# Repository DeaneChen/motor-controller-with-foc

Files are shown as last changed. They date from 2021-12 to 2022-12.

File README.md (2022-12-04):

<!--
 * @Author       : LuHeQiu
 * @Date         : 2021-12-08 13:26:15
 * @LastEditTime : 2022-12-04 19:14:46
 * @LastEditors  : LuHeQiu
 * @Description  : 
 * @FilePath     : \motor-controller-with-foc\README.md
 * HomePage     : https://luheqiu.com
-->
<div align="center">
    <br/>
    <h1>
        <a href="https://www.luheqiu.com" target="_blank" rel="noopener noreferrer">
        LuHeQiu Logo
        </a>
    </h1>
    <strong>路何求创想工坊出品 | 硬件&算法工坊</strong>
</div>

# 【FOC+STM32】双路直流无刷电机矢量控制器-使用文档

<p align="center">
    
    
    
    
    
</p>

## 📕 介绍
控制器主控芯片采用STM32F405RGT6，控制器底层基于HAL库和FreeRTOS实时操作系统，预留CAN、USART、SWD、USB接口各一，便于通信和控制的工程应用。该控制器提供双路无刷电机控制，同时分别预留编码器接口与电压采样接口，适合于有感FOC与无感FOC的控制应用或算法验证。同时该控制板还可以适合于异步电机的矢量控制。

> **注意：此项目为硬件设计与算法验证项目，当前正处于设计和验证阶段，未进行完善的工程应用测试和极限参数的压力测试，请勿直接使用，以避免出现安全问题和财产损失，后续的验证情况会同步更新**

### 演示图片

<p align="center">
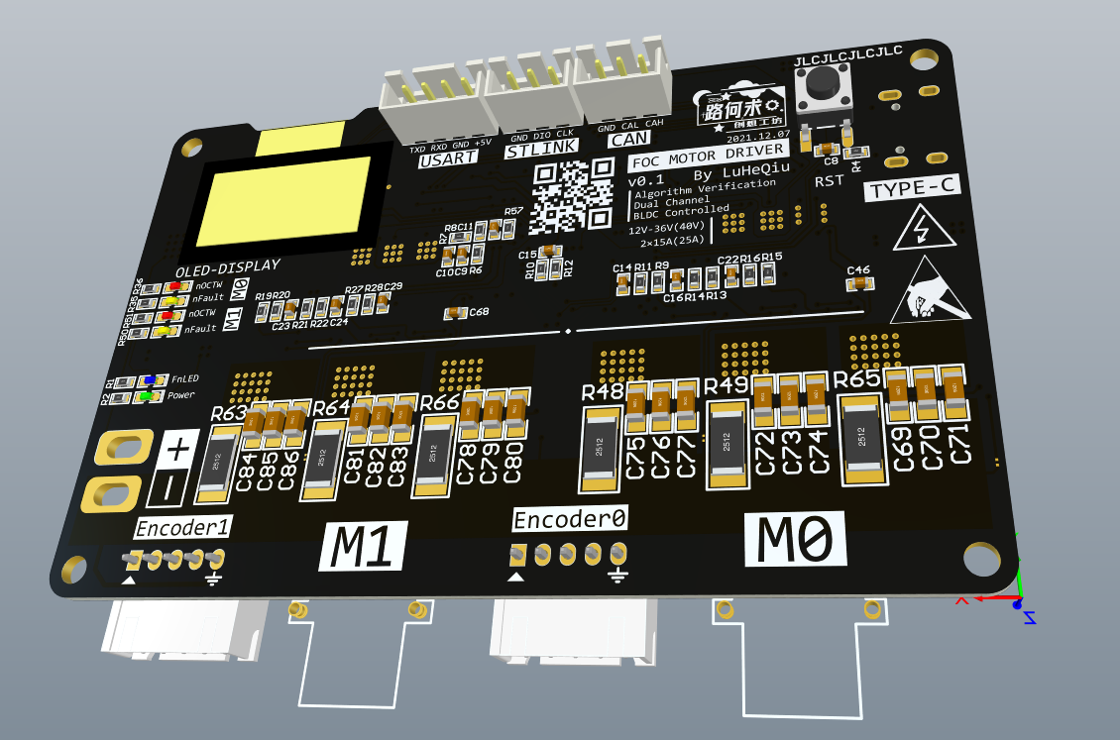
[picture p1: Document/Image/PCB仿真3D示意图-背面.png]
PCB仿真3D示意图-背面
    
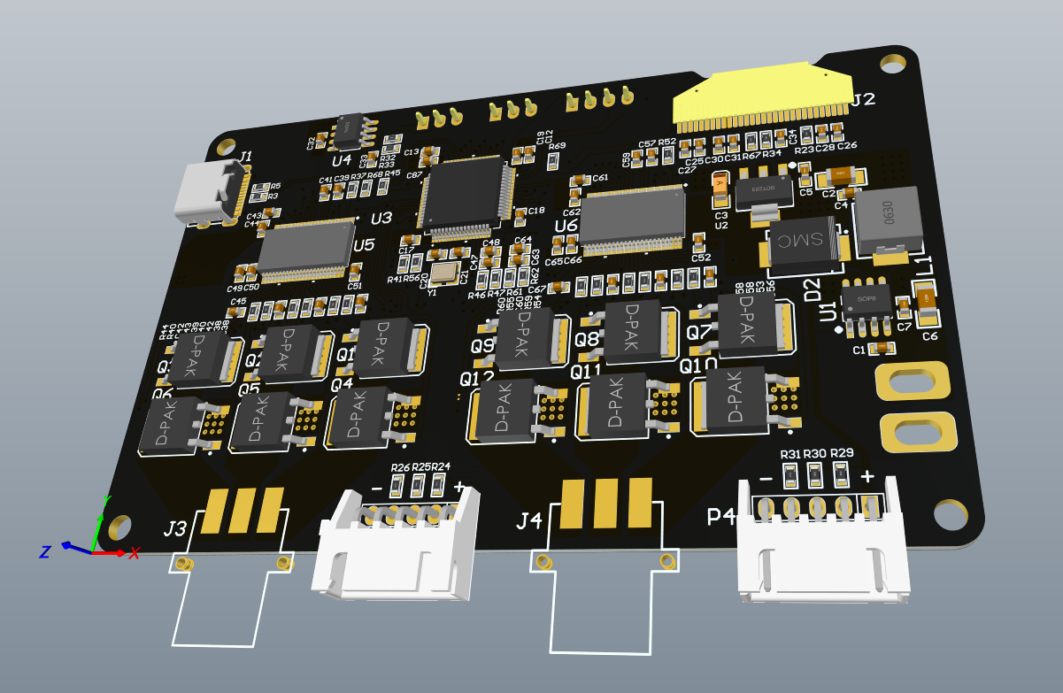
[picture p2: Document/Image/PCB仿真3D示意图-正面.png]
PCB仿真3D示意图-正面
    
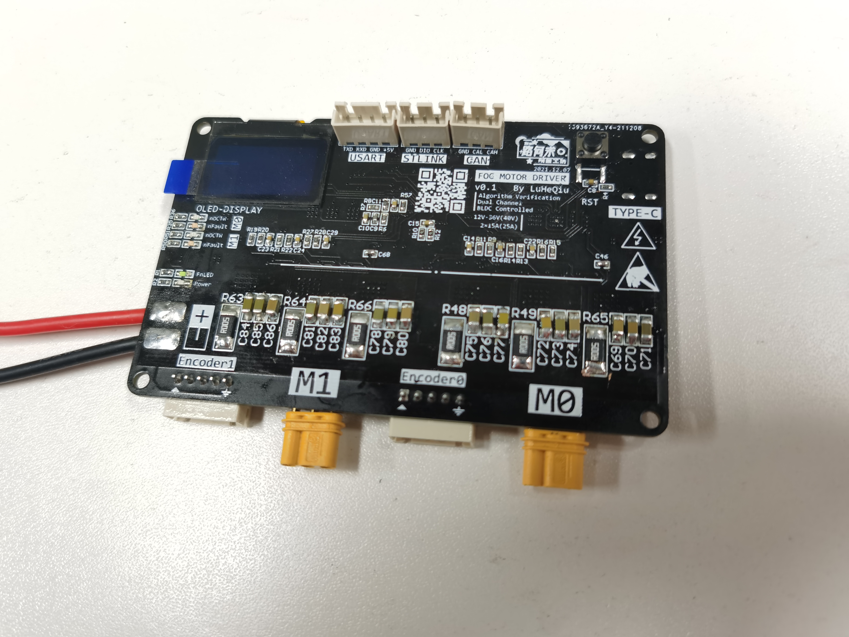
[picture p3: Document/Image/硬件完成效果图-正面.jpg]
    
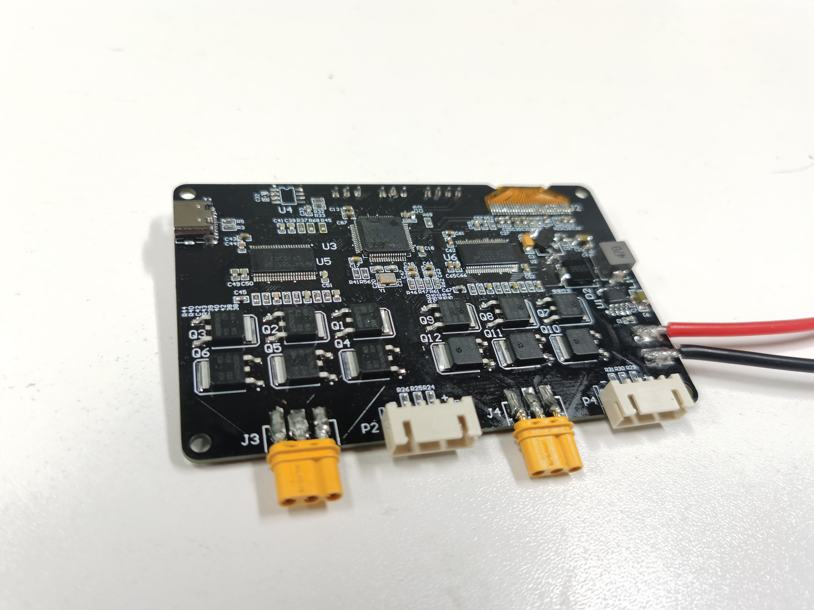
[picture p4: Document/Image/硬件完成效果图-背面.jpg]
    
</p>

### 什么是FOC
FOC，即Field Oriented Control的缩写，可以译为磁场定向控制或矢量控制。是一种针对异步电机或直流无刷电机的变频调速方式，具有以下几个特点：
+ 调速范围宽，具有良好低速特性与高速特性
+ 机械特性硬，转速稳定性好
+ 速度可以在整个调速范围内连续控制，平滑性好，可以实现无级调速
+ 可以实现力矩控制与力矩反馈
+ 结构复杂，算法复杂，贵

## 🎬 进度

### 日志

详见： [日志文档](./LOG.md "日志文档")

 [ **【2021.12.27】 焊接完成** ](./LOG.md/#20211227-焊接完成 "焊接完成")

[ **【2021.01.09】 查找到两个硬件BUG** ](./LOG.md/#20220113-屏幕驱动编写完成 "查找到两个硬件BUG")

[ **【2021.01.13】 屏幕驱动编写完成** ](./LOG.md/#20220113-屏幕驱动编写完成 "屏幕驱动编写完成")

## ✨ 参数

+ **规格**
    - 体积: 99.0mm × 71.5mm × 8.8mm

+ **性能**
    - 额定电压 **12V - 36V**
    - **双路**直流无刷电机驱动
    - 最大持续电流 **2 × 15A**
    - **支持**三相霍尔编码器（可根据需要选择性焊接上拉电阻）
    - **支持**最大不超过3PIN的数字编码器或其他编码器（如PWM信号的AS5600）
    - **不支持**需要ADC采样的模拟编码器

+ **功能**
    - 一个可编程LED灯，一个电源指示灯，四个电机状态指示灯
    - 板载 OLED 屏显（基于带片选的SPI通信）
    - 基于 2 × DRV8303 的双路电机驱动（与OLED共用SPI总线）
    - 提供 2 x 3 的UVW电压采样
    - 提供 2 x 2 的电流采样，分别为V相和W相

+ **接口**
    - CAN x 1
    - USART x 1
    - TYPE-C USB接口 x 1 (FS全速接口，不支持OTG，不支持供电)

## 📄 BOM表

<details>

**<summary>FOC_Controller_BOM**</summary>

| Comment | Value | Designator | Quantity | Footprint | LibRef | Description | Price/pcs | Price |
|---|---|---|---|---|---|---|---|---|
| Cap | 1μF | "C1, C4, C7, C30, C43, C44, C61, C62" | 8 | C 0603\_L | Cap | Capacitor | 0\.0031 | 0\.0248 |
| Cap Pol1 | 100μF | C2 | 1 | C 1206\_M | Cap Pol1 | Polarized Capacitor \(Radial\) | 0\.2 | 0\.2 |
| Cap Pol1 | 22μF | C3 | 1 | CD A\(3216\) | Cap Pol1 | Polarized Capacitor \(Radial\) | 0\.749 | 0\.749 |
| Cap | 10μF | C5 | 1 | C 0603\_M | Cap | Capacitor | 0\.0853 | 0\.0853 |
| Cap Pol1 | 47μF | C6 | 1 | C 1206\_M | Cap Pol1 | Polarized Capacitor \(Radial\) | 0\.2 | 0\.2 |
| Cap | 100nF | "C8, C15, C17, C18, C19, C32, C51, C52, C87" | 9 | C 0603\_L | Cap | Capacitor | 0\.0134 | 0\.1206 |
| Cap | 0\.01μF | C9 | 1 | C 0603\_L | Cap | Capacitor | 0\.0131 | 0\.0131 |
| Cap | 0\.1μF | "C10, C11, C14, C16, C22, C23, C24, C29, C38, C40, C42, C50, C56, C58, C60, C66" | 16 | C 0603\_L | Cap | Capacitor | 0\.0134 | 0\.2144 |
| Cap | 2\.2μF | "C12, C13, C26, C39, C57" | 5 | C 0603\_L | Cap | Capacitor | 0\.186 | 0\.93 |
| Cap | 20pF | "C20, C21" | 2 | C 0603\_L | Cap | Capacitor | 0\.025 | 0\.05 |
| Cap | 4\.7μF 16V X7R | C25 | 1 | C 0603\_L | Cap | Capacitor | 0\.1 | 0\.1 |
| Cap | 1μF 16V X5R | C27 | 1 | C 0603\_L | Cap | Capacitor | 0\.031 | 0\.031 |
| Cap | 4\.7μF | "C28, C34, C49, C65" | 4 | C 0603\_L | Cap | Capacitor | 0\.1 | 0\.4 |
| Cap | 1μF 16V | C31 | 1 | C 0603\_L | Cap | Capacitor | 0\.031 | 0\.031 |
| Cap | 47nF | C33 | 1 | C 0603\_L | Cap | Capacitor | 0\.025 | 0\.025 |
| Cap | 0\.022μF | "C41, C59" | 2 | C 0603\_L | Cap | Capacitor | 0\.025 | 0\.05 |
| Cap | 1000pF | "C45, C46, C67, C68" | 4 | C 0603\_L | Cap | Capacitor | 0\.025 | 0\.1 |
| Cap | 2200pF | "C47, C48, C63, C64" | 4 | C 0603\_L | Cap | Capacitor | 0\.025 | 0\.1 |
| Cap | 100μF | "C69, C70, C71, C72, C73, C74, C75, C76, C77, C78, C79, C80, C81, C82, C83, C84, C85, C86" | 18 | C 1206\_M | Cap | Capacitor | 0\.2 | 3\.6 |
| BLUE\_LED | | D1 | 1 | LED 0603B | LED2 | "Typical RED, GREEN, YELLOW, AMBER GaAs LED" | 0\.07 | 0\.07 |
| SS56 | | D2 | 1 | SMC | Diode BAS70 | Silicon AF Schottky Diode for High\-Speed Switching | 0\.4847 | 0\.4847 |
| GREEN\_LED | | D3 | 1 | LED 0603G | LED2 | "Typical RED, GREEN, YELLOW, AMBER GaAs LED" | 0\.04 | 0\.04 |
| YELLOW\_LED | | "D4, D6" | 2 | LED 0603Y | LED2 | "Typical RED, GREEN, YELLOW, AMBER GaAs LED" | 0\.045 | 0\.09 |
| RED\_LED | | "D5, D7" | 2 | LED 0603R | LED2 | "Typical RED, GREEN, YELLOW, AMBER GaAs LED" | 0\.045 | 0\.09 |
| USB\-C | | J1 | 1 | USB\-C\-SMD\_TYPE\-C\-USB\-5 | USB\-C/S | USB\-C型母接口 | 0\.4844 | 0\.4844 |
| OLED 128\*64 | | J2 | 1 | OLED 0\.96'' 128x64 | Header 30 | "Header, 30\-Pin" | 9\.75 | 9\.75 |
| 三相连接器\-插座 | | "J3, J4" | 2 | MR30PW\-M | 三相连接器\-插座 | | 2\.1 | 4\.2 |
| Inductor | 47μH/3A | L1 | 1 | L\-SMD\-0630 | Inductor | Inductor | 0\.7579 | 0\.7579 |
| USART | | P1 | 1 | SIPA04 | Header 4 | "Header, 4\-Pin" | 0\.04 | 0\.04 |
| M0\_Encoder | | P2 | 1 | SIPB05 | Header 5 | "Header, 5\-Pin" | 0\.06 | 0\.06 |
| CAN | | P3 | 1 | SIPA03 | Header 3 | "Header, 3\-Pin" | 0\.03 | 0\.03 |
| M1\_Encoder | | P4 | 1 | SIPB05 | Header 5 | "Header, 5\-Pin" | 0\.06 | 0\.06 |
| STLINK | | P5 | 1 | SIPA03 | Header 3 | "Header, 3\-Pin" | 0\.03 | 0\.03 |
| KIA50N03BD | | "Q1, Q2, Q3, Q4, Q5, Q6, Q7, Q8, Q9, Q10, Q11, Q12" | 12 | TO252 \- 3 | N\-MOSFET | | 0\.574 | 6\.888 |
| Res2 | 1K | "R1, R35, R36, R50, R51" | 5 | R 0603\_L | Res2 | Resistor | 0\.006 | 0\.03 |
| Res2 | 12K | R2 | 1 | R 0603\_L | Res2 | Resistor | 0\.006 | 0\.006 |
| Res2 | 22Ω | "R3, R5" | 2 | R 0603\_L | Res2 | Resistor | 0\.005974 | 0\.011948 |
| Res2 | 4\.7K | "R4, R24, R25, R26, R29, R30, R31, R41, R45, R56, R57, R68, R69" | 13 | R 0603\_L | Res2 | Resistor | 0\.006 | 0\.078 |
| Res2 | 43K | "R6, R9, R13, R15, R19, R21, R27" | 7 | R 0603\_L | Res2 | Resistor | 0\.006 | 0\.042 |
| Res2 | 3\.3Ω | R7 | 1 | R 0603\_L | Res2 | Resistor | 0\.009572 | 0\.009572 |
| Res2 | 3\.9K | "R8, R11, R14, R16, R20, R22, R28" | 7 | R 0603\_L | Res2 | Resistor | 0\.006 | 0\.042 |
| Res2 | 0Ω | "R10, R12" | 2 | R 0603\_L | Res2 | Resistor | 0\.006 | 0\.012 |
| Res2 | 910KΩ | R23 | 1 | R 0603\_L | Res2 | Resistor | 0\.006 | 0\.006 |
| Res2 | 60Ω | "R32, R33" | 2 | R 0603\_L | Res2 | Resistor | 0\.010254 | 0\.020508 |
| Res2 | 4\.7KΩ | "R34, R67" | 2 | R 0603\_L | Res2 | Resistor | 0\.006 | 0\.012 |
| Res2 | 1Ω | "R37, R52" | 2 | R 0603\_L | Res2 | Resistor | 0\.006207 | 0\.012414 |
| Res2 | 10 | "R38, R39, R40, R42, R43, R44, R53, R54, R55, R58, R59, R60" | 12 | R 0603\_L | Res2 | Resistor | 0\.006736 | 0\.080832 |
| Res2 | 56Ω | "R46, R47, R61, R62" | 4 | R 0603\_L | Res2 | Resistor | 0\.006778 | 0\.027112 |
| Res2 | 0\.005Ω 4W | "R48, R49, R63, R64, R65, R66" | 6 | R 2512\_M | Res2 | Resistor | 0\.006 | 0\.036 |
| SW\-PB | | S1 | 1 | TSW SMD\-6\*6\*5 | SW\-PB | Switch | 0\.2679 | 0\.2679 |
| XL2011 | | U1 | 1 | SOP8\_N | XL2011 | 5V/2\.1A DC\-DC Buck电源芯片\(<50V\) | 1\.9728 | 1\.9728 |
| CJT1117\-3\.3 | | U2 | 1 | SOT223\_N | Volt Reg | Voltage Regulator | 0\.6873 | 0\.6873 |
| STM32F405RGT6 | | U3 | 1 | LQFP64\-10x10mm | STM32F405RGT6 | No Description Available | 45 | 45 |
| TJA1040 | | U4 | 1 | SOP8\_N | TJA1040 | CAN收发器 | 9\.02 | 9\.02 |
| DRV8303 | | "U5, U6" | 2 | DCA48\_4P42X3P48 | DRV8303 | "THREE PHASE PRE\-DRIVER WITH DUAL CURRENT SHUNT AMPLIFIERS, DCA0048A" | 20 | 40 |
| 8MHz | | Y1 | 1 | OSC 3225\-4P | XTAL | Crystal Oscillator | 1\.9989 | 1\.9989 |
| | | | | | | | | |
| | | | | | | | Total | 129\.472486 |

</details>

## 🚀 快速上手
1. 可使用AD软件打开 *FOC_Controller.PcbDoc* 文件，根据需要进行修改或生成Gerber文件发送给PCB板厂进行制作。工艺为四层板，建议外层铜厚1oz及以上，内层铜厚0.5oz及以上。
2. 使用趁手的焊台进行焊接。
3. 检查焊接与上电是否正常。
4. 进行FOC控制代码的设计与验证。（或等我更新）

## 📧 联系我
如有未尽事宜或其他合理问题，可以通过电子邮件联系我
电子邮箱：<Deane_Chen@foxmail.com>
个人网站：<https://www.luheqiu.com>

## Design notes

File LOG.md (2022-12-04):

<!--
 * @Author       : LuHeQiu
 * @Date         : 2022-01-13 17:05:55
 * @LastEditTime : 2022-12-04 19:08:12
 * @LastEditors  : LuHeQiu
 * @Description  : 
 * @FilePath     : \motor-controller-with-foc\LOG.md
 * @HomePage     : https://www.luheqiu.com
-->

<div align="center">
    <br/>
    <h1>
        <a href="https://www.luheqiu.com" target="_blank" rel="noopener noreferrer">
        LuHeQiu Logo
        </a>
    </h1>
    <strong>路何求创想工坊出品 | 硬件&算法工坊</strong>
</div>

# 【FOC+STM32】双路直流无刷电机矢量控制器-维护日志

## LOG

<span id="2021-12-27">

### [2021.12.27] 焊接完成

</span>

前段时间完成了初步的焊接工作，并在焊接过程和焊接完成的电气测试中发现如下问题：

1. CJT1117引脚映射错误，具体为：2→3，3→1，1→2。本次为了先行验证整体是否可行，并寻找更多错误，通过旋转CJT1117芯片45°强行修改。实际制作等待 v0.2 版本进行调整。
2. KIA50N03的漏源耐压是30V，因此额定电压建议20V以下。如果需要30V以上的驱动电压，应当更换为KIA50N06。这个是我买错了，KIA50N06的耐压是60V。这两款MOSFET我均已购买，等后续性能测试再看看是否好用，不好用再换。（个人感觉这两款MOSFET都好便宜，每片不到1元。）
3. 此款128x64的OLED屏幕，可以使用 3 - wire SPI 进行通信，即片选CS、时钟SCK和数据MOSI。但是，在编写点灯代码（进行能否运行的可行性测试）的时候，仔细看了一下OLED数据手册，发现如果使用3线SPI通信，它的协议是非标的。OLED每帧数据需要九个时钟，传输九个比特，后面八位为传输的一个字节，第一位用于决定这个字节是命令还是数据。这就很难受了，这意味着我难以使用STM32的硬件SPI，也难以使用 “DMA+中断” 的方式进行数据传输，我需要使用软件模拟SPI接口，这一方面多占用了CPU，另一方面也浪费了为特地为通信留出来的支持配置为硬件SPI的引脚IO。**这说明：硬件设计也需要考虑数据手册的软件部分**
4. LED灯的丝印处，nOCTW和nFault的位置交换了。

顺带吐槽一句，不知道是因为黑色焊油的问题还是我焊接手法的问题，感觉这个板子的焊油层很容易磨掉啊，好几处都露出铜皮了。（还是说是某创板的问题？）

<span id="2022-01-09">

### [2022.01.09] 查找到两个硬件BUG

</span>

**BUG1:** 修复了主电源的问题

1. 在烧录代码的过程中，keil一直提示internal command error。但是从设置界面是可以读取到芯片的。之前也遇到过这种情况，一般通过重新插拔、上电均可解决，但这次不行。

2. 伴随着发现用手轻轻按压板子正面绝缘处会发现掉电，而轻轻按压板子背面不发生掉电。

3. 经筛查，掉电为DCDC开关电源芯片XL2011输出电压降至0.6 ~ 0.7V。此外，如果在板子5V接口处挂上负载，则无法正常上电，输出同样为0.6 ~ 0.7V，移开负载正常。如果空载则能够正常上电，5V成功输出后，挂上负载也能正常工作。

4. 通过更换XL2011输入输出侧的电容，按压板子使之掉电的情况缓解了一会儿，但随后又马上恢复原状。

5. 考虑是电源问题。初步怀疑是XL2011的质量，后发现是布板失误。下图黑色框框处分别为肖特基二极管的阳极和XL2011的7脚与8脚。此为经典的异步整流BUCK电路，D1提供电流回路，且频率较高，此处电流应当快速回至XL2011的地。其回路应当极可能短且尽可能小。

6. 通过旋转二极管和导线跳线使得输出电容负极和二极管阳极所接GND均尽快返回芯片的GND后，上述所有问题恢复正常。

<p align="center">
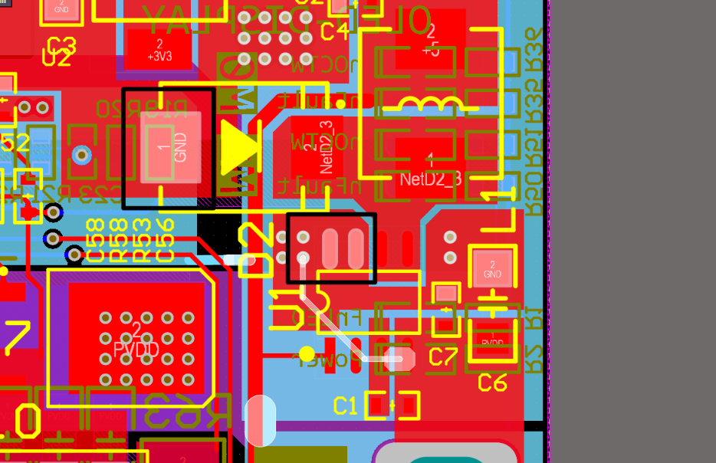
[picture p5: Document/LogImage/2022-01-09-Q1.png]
    
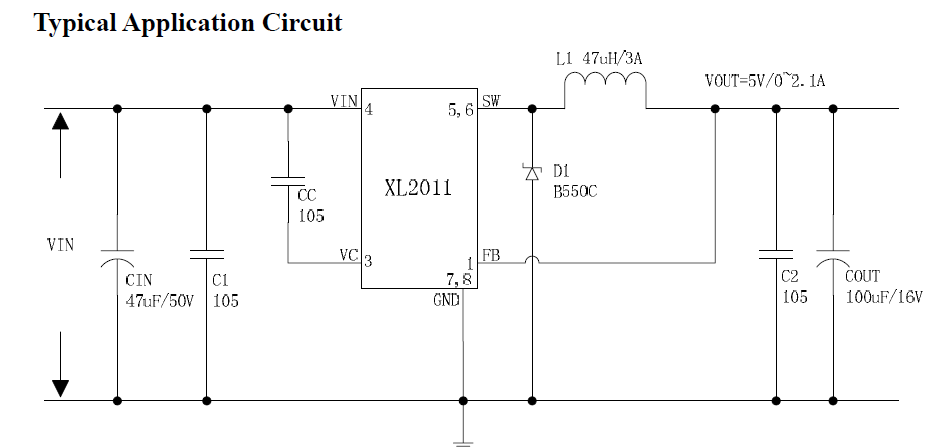
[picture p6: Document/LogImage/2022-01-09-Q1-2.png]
    
</p>

6. 此处使用的二极管为SS56，平均输出整流电流可达5A，而实际上后级负载的电流几乎不超过100mA，即便挂上两路编码器和通讯负载也会不会超过200mA，使用SS56和XL2011过于浪费，且SS56封装庞大，占用过大的版面空间。可以更换为其他300 - 400mA左右的肖特基二极管。

7. v0.2电路将不使用XL2011，而使用其他的国产同步整流芯片。在提高效率的同时，省去肖特基二极管。

**BUG2:** 查找出了5V供电支路的问题

1. 在掉电问题中，更换电容初步缓解后，从远离开关电源的5V口可以带负载上电。而靠近开关电源的5V口仍然上电失败，开关芯片输出为0.6 ~ 0.7V。下图中，可以看到5V供电回路是从XL2011的输出脚和反馈脚之间的反馈回路引出的，这可能导致反馈出现问题使得降压输出失败。虽然通过上述BUG1的修复不再出现问题，但后续设计中也应当避免。

<p align="center">
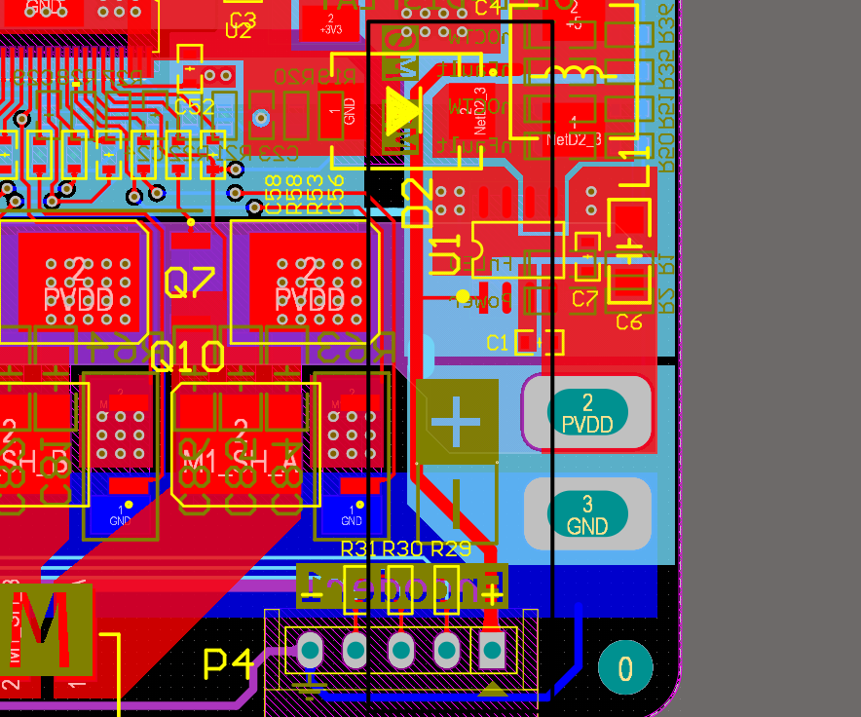
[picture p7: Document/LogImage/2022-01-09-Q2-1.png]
    
</p>

<span id="2022-01-13"> 

### [2022.01.13] 屏幕驱动编写完成

</span>

1. 完成了显示器屏幕驱动的编写，该部分代码分为三部分:
    + 通讯层 spi.c
    + 驱动层 screen_drive.c
    + GUI 层 lgui.c

2. 按照面向对象的思路进行逐层封装，以高内聚低耦合的原则进行了重构。以前用OLED或者SPI的屏幕驱动都是用商家的例程，着实有点不方便。特别是OLED，无法做到任意坐标随心随意的显示。

3. 三个层之间仅仅通过一两个API接口进行连接。

4. lgui.c实现了绘制点、矩形、图片和格式化字符输出。其中，格式化字符有类似于C语言printf的语法。提供%d、%3d、%.2f等格式的输入。

<p align="center">
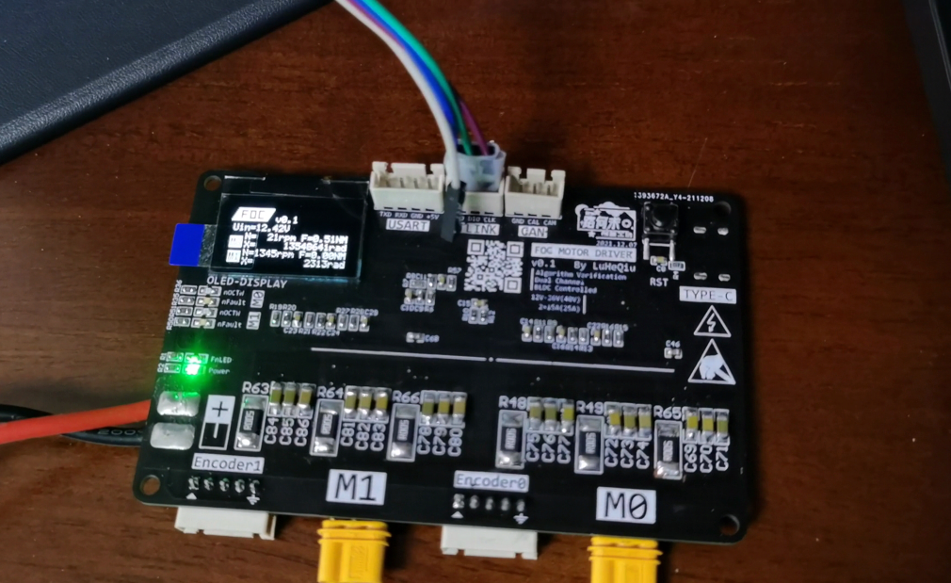
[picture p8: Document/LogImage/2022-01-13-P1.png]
    
</p>

<span id="2022-12-04"> 

### [2022.12.04] FOC控制部分的开环回路完成

</span>

1. 完成了FOC控制部分的开环回路，该部分代码分为:
    + Park变换和Park反变换
    + Clarke变换
    + SVPWM算法

2. 对比了矩阵变换整合与幅角直接计算的SVPWM算法的速度
    + 矩阵变换方式（本工程目前所使用的）：10万次40ms
    + 幅角直接计算：10万次240ms

    虽然10万次运算240ms，运算一次2.4μs看起来也绰绰有余，但考虑到我期望设计的FOC控制周期在5KHz以上且尽可能更高（初步想法，后面有没有问题再说），还是打算尽可能节约时间。

3. 修复了一下数据上报的BUG、在上位机看寄存器回报值缺了高位零，不是很舒服，例如0x08只上报了0x8

4. 在设计变换函数的时候，需要用到Sin函数，本来打算直接查表法，发现精度差了点意思，用了math.h库函数又嫌弃太慢（可能也不慢，因为我后面发现了是一些重复计算的问题）。后来尝试了一下基于插值的查表Sin函数，后面又发现大参数的三角函数会因为float乘法导致精度丢失，搜了不少论文，发现参数缩减是一个非常数学的问题，研究了半天发现计算有点大，遂放弃，优化到后面，好奇了一下DSP库的Sin函数怎么实现的，怎么解决大参数缩减的问题，结果发现DSP库也是基于插值的查表法（笑哭），所以这算是重复造轮子吗？233。最后没有解决大参数问题，将就用了。

    速度对比：
    + 查表法：100万次167ms
    + 插值后的查表法：100万次350ms
    + DSP库：100万次337ms
    + Math库（解决了大参数问题）：100万次1200ms

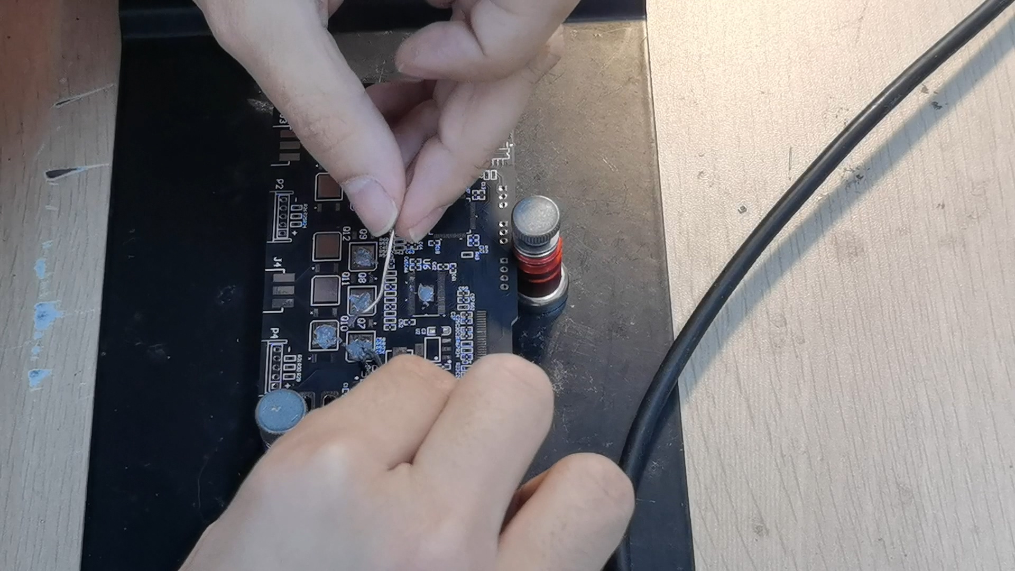
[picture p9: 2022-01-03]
Document/Image/焊接过程0.jpg

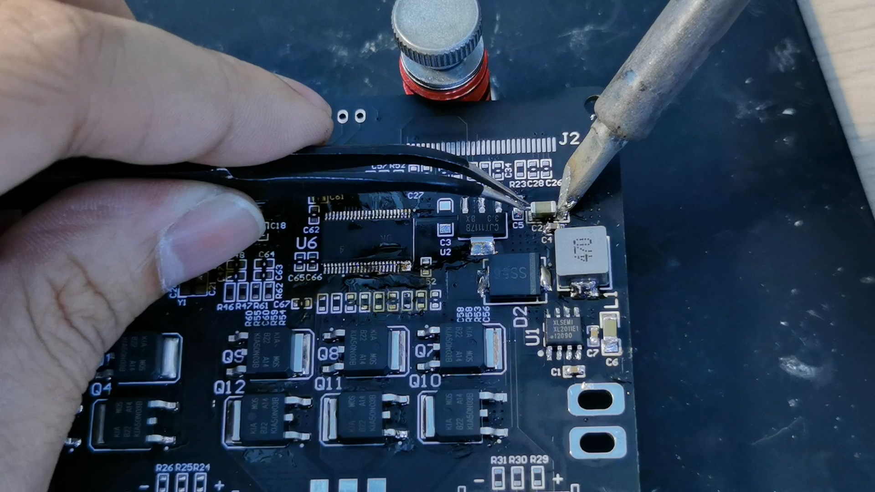
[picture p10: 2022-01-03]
Document/Image/焊接过程2.jpg

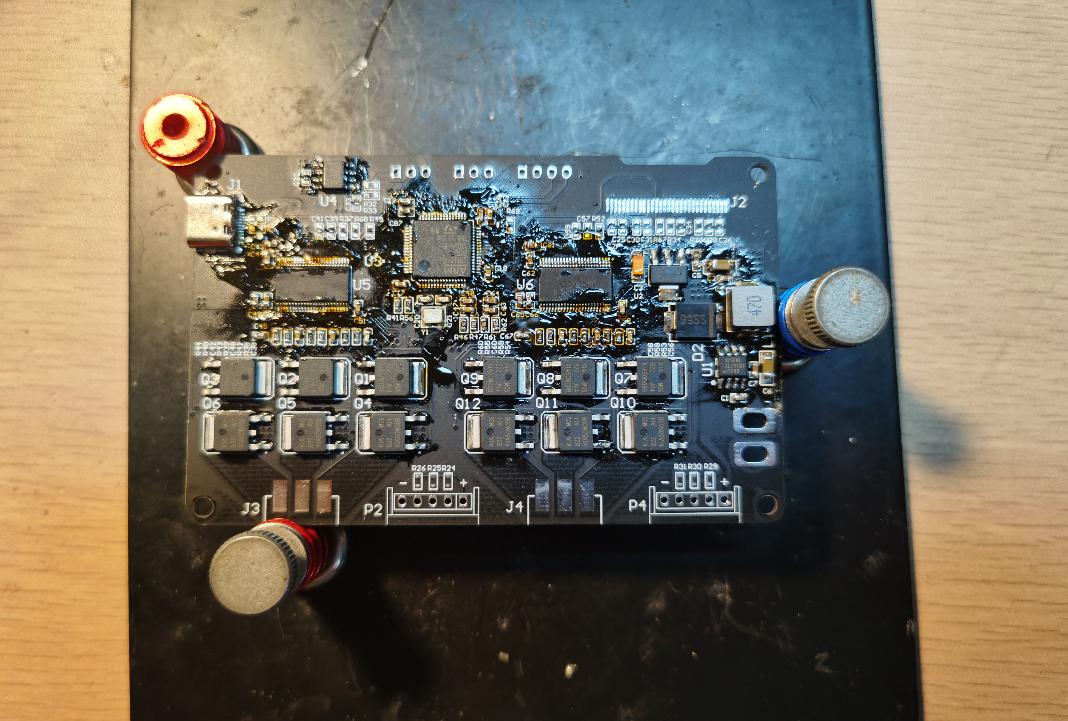
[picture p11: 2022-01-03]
Document/Image/焊接过程4.jpg

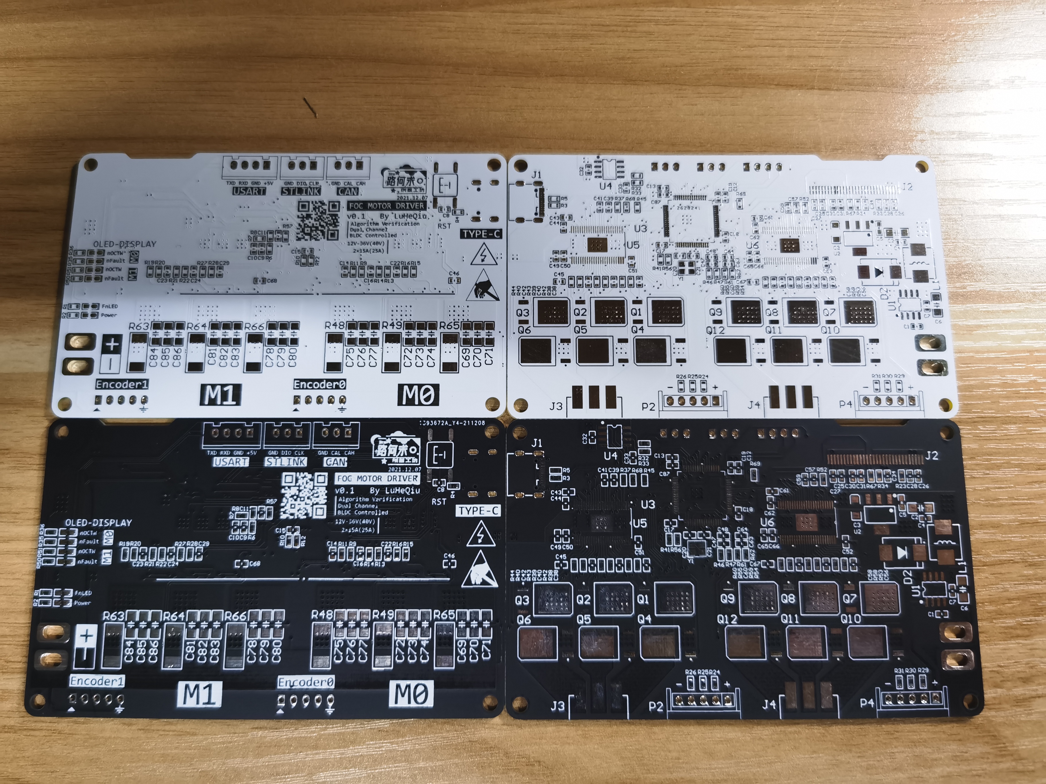
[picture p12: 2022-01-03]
Document/Image/PCB空板实物图.jpg

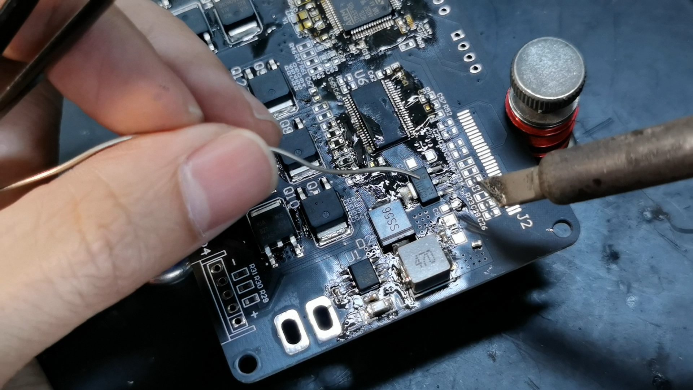
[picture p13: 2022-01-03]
Document/Image/焊接过程1.jpg

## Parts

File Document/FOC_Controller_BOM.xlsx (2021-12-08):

Comment | Value | Designator | Quantity | Footprint | LibRef | Description | Price/pcs | Price
Cap | 1μF | C1, C4, C7, C30, C43, C44, C61, C62 | 8 | C 0603_L | Cap | Capacitor | 0.0031 | 0.0248
Cap Pol1 | 100μF | C2 | 1 | C 1206_M | Cap Pol1 | Polarized Capacitor (Radial) | 0.2 | 0.2
Cap Pol1 | 22μF | C3 | 1 | CD A(3216) | Cap Pol1 | Polarized Capacitor (Radial) | 0.749 | 0.749
Cap | 10μF | C5 | 1 | C 0603_M | Cap | Capacitor | 0.0853 | 0.0853
Cap Pol1 | 47μF | C6 | 1 | C 1206_M | Cap Pol1 | Polarized Capacitor (Radial) | 0.2 | 0.2
Cap | 100nF | C8, C15, C17, C18, C19, C32, C51, C52, C87 | 9 | C 0603_L | Cap | Capacitor | 0.0134 | 0.1206
Cap | 0.01μF | C9 | 1 | C 0603_L | Cap | Capacitor | 0.0131 | 0.0131
Cap | 0.1μF | C10, C11, C14, C16, C22, C23, C24, C29, C38, C40, C42, C50, C56, C58, C60, C66 | 16 | C 0603_L | Cap | Capacitor | 0.0134 | 0.2144
Cap | 2.2μF | C12, C13, C26, C39, C57 | 5 | C 0603_L | Cap | Capacitor | 0.186 | 0.93
Cap | 20pF | C20, C21 | 2 | C 0603_L | Cap | Capacitor | 0.025 | 0.05
Cap | 4.7μF 16V X7R | C25 | 1 | C 0603_L | Cap | Capacitor | 0.1 | 0.1
Cap | 1μF 16V X5R | C27 | 1 | C 0603_L | Cap | Capacitor | 0.031 | 0.031
Cap | 4.7μF | C28, C34, C49, C65 | 4 | C 0603_L | Cap | Capacitor | 0.1 | 0.4
Cap | 1μF 16V | C31 | 1 | C 0603_L | Cap | Capacitor | 0.031 | 0.031
Cap | 47nF | C33 | 1 | C 0603_L | Cap | Capacitor | 0.025 | 0.025
Cap | 0.022μF | C41, C59 | 2 | C 0603_L | Cap | Capacitor | 0.025 | 0.05
Cap | 1000pF | C45, C46, C67, C68 | 4 | C 0603_L | Cap | Capacitor | 0.025 | 0.1
Cap | 2200pF | C47, C48, C63, C64 | 4 | C 0603_L | Cap | Capacitor | 0.025 | 0.1
Cap | 100μF | C69, C70, C71, C72, C73, C74, C75, C76, C77, C78, C79, C80, C81, C82, C83, C84, C85, C86 | 18 | C 1206_M | Cap | Capacitor | 0.2 | 3.6
BLUE_LED |  | D1 | 1 | LED 0603B | LED2 | Typical RED, GREEN, YELLOW, AMBER GaAs LED | 0.07 | 0.07
SS56 |  | D2 | 1 | SMC | Diode BAS70 | Silicon AF Schottky Diode for High-Speed Switching | 0.4847 | 0.4847
GREEN_LED |  | D3 | 1 | LED 0603G | LED2 | Typical RED, GREEN, YELLOW, AMBER GaAs LED | 0.04 | 0.04
YELLOW_LED |  | D4, D6 | 2 | LED 0603Y | LED2 | Typical RED, GREEN, YELLOW, AMBER GaAs LED | 0.045 | 0.09
RED_LED |  | D5, D7 | 2 | LED 0603R | LED2 | Typical RED, GREEN, YELLOW, AMBER GaAs LED | 0.045 | 0.09
USB-C |  | J1 | 1 | USB-C-SMD_TYPE-C-USB-5 | USB-C/S | USB-C型母接口 | 0.4844 | 0.4844
OLED 128*64 |  | J2 | 1 | OLED 0.96'' 128x64 | Header 30 | Header, 30-Pin | 9.75 | 9.75
三相连接器-插座 |  | J3, J4 | 2 | MR30PW-M | 三相连接器-插座 |  | 2.1 | 4.2
Inductor | 47μH/3A | L1 | 1 | L-SMD-0630 | Inductor | Inductor | 0.7579 | 0.7579
USART |  | P1 | 1 | SIPA04 | Header 4 | Header, 4-Pin | 0.04 | 0.04
M0_Encoder |  | P2 | 1 | SIPB05 | Header 5 | Header, 5-Pin | 0.06 | 0.06
CAN |  | P3 | 1 | SIPA03 | Header 3 | Header, 3-Pin | 0.03 | 0.03
M1_Encoder |  | P4 | 1 | SIPB05 | Header 5 | Header, 5-Pin | 0.06 | 0.06
STLINK |  | P5 | 1 | SIPA03 | Header 3 | Header, 3-Pin | 0.03 | 0.03
KIA50N03BD |  | Q1, Q2, Q3, Q4, Q5, Q6, Q7, Q8, Q9, Q10, Q11, Q12 | 12 | TO252 - 3 | N-MOSFET |  | 0.574 | 6.888
Res2 | 1K | R1, R35, R36, R50, R51 | 5 | R 0603_L | Res2 | Resistor | 0.006 | 0.03
Res2 | 12K | R2 | 1 | R 0603_L | Res2 | Resistor | 0.006 | 0.006
Res2 | 22Ω | R3, R5 | 2 | R 0603_L | Res2 | Resistor | 0.005974 | 0.011948
Res2 | 4.7K | R4, R24, R25, R26, R29, R30, R31, R41, R45, R56, R57, R68, R69 | 13 | R 0603_L | Res2 | Resistor | 0.006 | 0.078
Res2 | 43K | R6, R9, R13, R15, R19, R21, R27 | 7 | R 0603_L | Res2 | Resistor | 0.006 | 0.042
Res2 | 3.3Ω | R7 | 1 | R 0603_L | Res2 | Resistor | 0.009572 | 0.009572
Res2 | 3.9K | R8, R11, R14, R16, R20, R22, R28 | 7 | R 0603_L | Res2 | Resistor | 0.006 | 0.042
Res2 | 0Ω | R10, R12 | 2 | R 0603_L | Res2 | Resistor | 0.006 | 0.012
Res2 | 910KΩ | R23 | 1 | R 0603_L | Res2 | Resistor | 0.006 | 0.006
Res2 | 60Ω | R32, R33 | 2 | R 0603_L | Res2 | Resistor | 0.010254 | 0.020508
Res2 | 4.7KΩ | R34, R67 | 2 | R 0603_L | Res2 | Resistor | 0.006 | 0.012
Res2 | 1Ω | R37, R52 | 2 | R 0603_L | Res2 | Resistor | 0.006207 | 0.012414
Res2 | 10 | R38, R39, R40, R42, R43, R44, R53, R54, R55, R58, R59, R60 | 12 | R 0603_L | Res2 | Resistor | 0.006736 | 0.080832
Res2 | 56Ω | R46, R47, R61, R62 | 4 | R 0603_L | Res2 | Resistor | 0.006778 | 0.027112
Res2 | 0.005Ω 4W | R48, R49, R63, R64, R65, R66 | 6 | R 2512_M | Res2 | Resistor | 0.006 | 0.036
SW-PB |  | S1 | 1 | TSW SMD-6*6*5 | SW-PB | Switch | 0.2679 | 0.2679
XL2011 |  | U1 | 1 | SOP8_N | XL2011 | 5V/2.1A DC-DC Buck电源芯片(<50V) | 1.9728 | 1.9728
CJT1117-3.3 |  | U2 | 1 | SOT223_N | Volt Reg | Voltage Regulator | 0.6873 | 0.6873
STM32F405RGT6 |  | U3 | 1 | LQFP64-10x10mm | STM32F405RGT6 | No Description Available | 45 | 45
TJA1040 |  | U4 | 1 | SOP8_N | TJA1040 | CAN收发器 | 9.02 | 9.02
DRV8303 |  | U5, U6 | 2 | DCA48_4P42X3P48 | DRV8303 | THREE PHASE PRE-DRIVER WITH DUAL CURRENT SHUNT AMPLIFIERS, DCA0048A | 20 | 40
8MHz |  | Y1 | 1 | OSC 3225-4P | XTAL | Crystal Oscillator | 1.9989 | 1.9989
 |  |  |  |  |  |  | Total | 129.472486

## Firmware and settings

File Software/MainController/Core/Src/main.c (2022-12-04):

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
/* Includes ------------------------------------------------------------------*/
#include "main.h"
#include "adc.h"
#include "tim.h"
#include "usart.h"
#include "usb_device.h"
#include "gpio.h"

/* USER CODE BEGIN Includes */
#include "screen_drive.h"
#include "spi.h"
#include "led.h"
#include "lgui.h"
#include "picture.h"
#include "usbd_cdc_if.h"
#include "command.h"
#include "function.h"
#include "foc.h"
/* USER CODE END Includes */


/* USER CODE BEGIN PV */
__IO float add, mul;
__IO Vector2 U_target_ab;
__IO Vector3 T_target_uvw;
/* USER CODE END PV */

void SystemClock_Config(void);
/**
  * @brief  The application entry point.
  * @retval int
  */
int main(void)
{
  /* MCU Configuration--------------------------------------------------------*/

  /* Reset of all peripherals, Initializes the Flash interface and the Systick. */
  HAL_Init();

  /* Configure the system clock */
  SystemClock_Config();

  /* Initialize all configured peripherals */
  MX_GPIO_Init();
  MX_USART3_UART_Init();
  MX_TIM6_Init();
  MX_ADC1_Init();
  MX_USB_DEVICE_Init();
  MX_TIM1_Init();
  /* USER CODE BEGIN 2 */
  led.OFF();
  oled.Init();
  HAL_GPIO_WritePin(M0_EN_GPIO_Port,M0_EN_Pin,GPIO_PIN_SET);
  HAL_GPIO_WritePin(M1_EN_GPIO_Port,M1_EN_Pin,GPIO_PIN_SET);
  
  
  HAL_TIM_PWM_Start(&htim1,TIM_CHANNEL_1);
  HAL_TIM_PWM_Start(&htim1,TIM_CHANNEL_2);
  HAL_TIM_PWM_Start(&htim1,TIM_CHANNEL_3);
  HAL_TIMEx_PWMN_Start(&htim1,TIM_CHANNEL_1);
  HAL_TIMEx_PWMN_Start(&htim1,TIM_CHANNEL_2);
  HAL_TIMEx_PWMN_Start(&htim1,TIM_CHANNEL_3);
  __HAL_TIM_SET_COMPARE(&htim1, TIM_CHANNEL_1, 0);
  __HAL_TIM_SET_COMPARE(&htim1, TIM_CHANNEL_2, 0);
  __HAL_TIM_SET_COMPARE(&htim1, TIM_CHANNEL_3, 0);  
  
  
  //oled.Draw(10, 10, 1);
  lgui.ShowPicture(0, 0, foc, 48, 16, 1); lgui.ShowString(48, 16, 8, 1, 1, (uint8_t*)"v0.1");

  lgui.Fill(3, 33, 16, 45, 1);
  lgui.Fill(3, 49, 16, 61, 1);
  lgui.ShowString(4, 44, 12, 0, 1, (uint8_t*)"M0");
  lgui.ShowString(4, 60, 12, 0, 1, (uint8_t*)"M1");

  lgui.ShowString(18, 36, 8, 1, 1, (uint8_t*)"N=%4drpm F=%1.2fNM", 21,0.51);
  lgui.ShowString(18, 45, 8, 1, 1, (uint8_t*)"X=%13drad",13548641);

  lgui.ShowString(18, 54, 8, 1, 1, (uint8_t*)"N=%4drpm F=%1.2fNM",1345,0.01);
  lgui.ShowString(18, 63, 8, 1, 1, (uint8_t*)"X=%13drad",2313);

  //lgui.ShowString(0, 30, 12, 1, 1, (uint8_t*)"A:%04d",20);

  /* USER CODE END 2 */

  /* Infinite loop */
  /* USER CODE BEGIN WHILE */
  while (1)
  {
    /* USER CODE END WHILE */

    /* USER CODE BEGIN 3 */
    
    U_target_ab = (Vector2){0.1, 0.0};
    /* SVPWM 算法一耗时测量 */
    for (int i = 0; i < 100000; i++){
      SVPWM(&U_target_ab, 0.8f, &T_target_uvw);
    }
    /* SVPWM 算法二耗时测量 */
    for (int i = 0; i < 100000; i++){
      SVPWM2(&U_target_ab, 0.8f, &T_target_uvw);
    }

    //led.Shift();
    //HAL_Delay(500);
    HAL_ADC_Start(&hadc1);
    if(HAL_ADC_PollForConversion(&hadc1,0xff)==HAL_OK){
      lgui.ShowString(4,26,8,1,1,(uint8_t*)"Uin=%2.2fV",3.3f*HAL_ADC_GetValue(&hadc1)/4096*12.026f);
    }
    //HAL_Delay(10);
    ParsingCommand();
  }
  /* USER CODE END 3 */
}

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
/* USER CODE BEGIN 4 */

void HAL_TIM_PeriodElapsedCallback(TIM_HandleTypeDef *htim)
{
   if(htim == &htim6){
     LED_PeriodElapsedCallback();
   }
}
/* USER CODE END 4 */
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


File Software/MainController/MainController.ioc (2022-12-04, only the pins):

Mcu.UserName=STM32F405RGTx
PA10.Signal=S_TIM1_CH3
PA11.Signal=USB_OTG_FS_DM
PA12.Signal=USB_OTG_FS_DP
PA13.Signal=SYS_JTMS-SWDIO
PA14.Signal=SYS_JTCK-SWCLK
PA4.Signal=ADCx_IN4
PA6.GPIO_Label=SPI_SDI
PA6.Signal=GPIO_Input
PA7.GPIO_Label=SPI_SDO
PA7.Signal=GPIO_Output
PA8.Signal=S_TIM1_CH1
PA9.Signal=S_TIM1_CH2
PB10.Signal=USART3_TX
PB11.Signal=USART3_RX
PB12.GPIO_Label=M1_CS
PB12.Signal=GPIO_Output
PB13.Signal=TIM1_CH1N
PB14.Signal=TIM1_CH2N
PB15.Signal=TIM1_CH3N
PB3.GPIO_Label=SPI_SCK
PB3.Signal=GPIO_Output
PC10.GPIO_Label=M0_EN
PC10.Signal=GPIO_Output
PC11.GPIO_Label=M1_EN
PC11.Signal=GPIO_Output
PC12.GPIO_Label=M0_CS
PC12.Signal=GPIO_Output
PC13-ANTI_TAMP.GPIO_Label=OLED_CS
PC13-ANTI_TAMP.Signal=GPIO_Output
PD2.GPIO_Label=FnLED
PD2.Signal=GPIO_Output
PH0-OSC_IN.Signal=RCC_OSC_IN
PH1-OSC_OUT.Signal=RCC_OSC_OUT

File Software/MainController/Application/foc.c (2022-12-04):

/*
 * @Author       : LuHeQiu
 * @Date         : 2022-01-21 21:17:31
 * @LastEditTime : 2022-12-04 18:59:36
 * @LastEditors  : LuHeQiu
 * @Description  : 
 * @FilePath     : \motor-controller-with-foc\Software\MainController\Application\foc.c
 * @HomePage     : https://www.luheqiu.com
 */
#include "foc.h"
#include "function.h"
#include "tim.h"
#include "math.h"

#ifdef FOC_USE_CAL_CORE_FLOAT
    #define SQRT3_NUM   1.73205080757f
    #define SQRT3_2_NUM 0.86602540378f
    #define SQRT3_3_NUM 0.57735026919f
#else
    #define SQRT3_NUM 17320508f
#endif

static float curTheta = 0.0f;

void FOC_ControllerTask(void){

    Vector2 U_target_qd = {0.1, 0.0};
    Vector2 U_target_ab;
    Vector3 T_target_uvw;
    curTheta += 0.06283185307f;
    if(curTheta > 31.4159265f){
        curTheta = 0.0f;
    }
    RevParkTransformaion(&U_target_qd, curTheta, &U_target_ab);
    SVPWM(&U_target_ab, 0.8f, &T_target_uvw);

    if (T_target_uvw.x1 > SVPWM_PERIOD)
        T_target_uvw.x1 = SVPWM_PERIOD;
    if (T_target_uvw.x2 > SVPWM_PERIOD)
        T_target_uvw.x2 = SVPWM_PERIOD;
    if (T_target_uvw.x3 > SVPWM_PERIOD)
        T_target_uvw.x3 = SVPWM_PERIOD;

    __HAL_TIM_SET_COMPARE(&htim1, TIM_CHANNEL_1, (uint16_t)T_target_uvw.x1);
    __HAL_TIM_SET_COMPARE(&htim1, TIM_CHANNEL_2, (uint16_t)T_target_uvw.x2);
    __HAL_TIM_SET_COMPARE(&htim1, TIM_CHANNEL_3, (uint16_t)T_target_uvw.x3);
    
}


/**
 * @brief  Clarke线性变换，将一个三相电流向量分解为二相正交向量
 *         基本公式为：
 *                      | I_alpha |       |  1    -1/2     -1/2     |       | Ia |
 *                      | I_beta  |   =   |  0   3^0.5/2  -3^0.5/2  |   x   | Ib |
 *                                                                          | Ic |
 * @param  input 被变换的三相电流向量，是一个三维的向量
 * @param  output 变换得到的二相正交电流向量，是一个二维的向量
 * @retval none
 */
void ClarkeTransformaion(Vector3 *input, Vector2 *output){
    Vector2* current_ab = output;
    /* 使用乘法 替代 除法 */
    current_ab->x1 = input->x1 - input->x2 * 0.5f         - input->x3 * 0.5f;
    current_ab->x2 = 0.0f      + input->x2 * SQRT3_2_NUM  - input->x3 * SQRT3_2_NUM;
}

/**
 * @brief  Park线性变换，将一个二相静止坐标系变换到二相旋转坐标系，实质上只是一个旋转矩阵。
 *         基本公式为：
 *                      | I_d |   =   |  cos(theta)  sin(theta)  |   x   | I_alpha | 
 *                      | I_q |       | -sin(theta)  cos(theta)  |       | I_beta  |
 * 
 * @param  input 被变换的二相静止电流向量
 * @param  theta 角度
 * @param  output 变换得到的二相旋转电流向量
 * @retval none
 */
void ParkTransformaion(Vector2 *input, Degree theta, Vector2 *output){
    Vector2* current_dq = output;
    float costheta = CosByLut(theta);
    float sintheta = SinByLut(theta);
    current_dq->x1 =  input->x1 * costheta + input->x2 * sintheta;
    current_dq->x2 = -input->x1 * sintheta + input->x2 * costheta;
}

/**
 * @brief  Park反变换，将一个二相旋转坐标系变换到二相静止坐标系，实质上只是一个逆向的旋转矩阵。
 *         基本公式为：
 *                      | U_alpha |   =   |  cos(theta) -sin(theta)  |   x   | U_d | 
 *                      | U_beta  |       |  sin(theta)  cos(theta)  |       | U_q |
 */
void RevParkTransformaion(Vector2 *input, Degree theta ,Vector2 *output){
    ParkTransformaion(input, 0 - theta, output);
}



//static const FOC8BitsType sector_code[7] = {0b100, 0b110, 0b010, 0b011, 0b001, 0b101, 0b100}; /* 扇区电压基向量编码表（已弃用） */
/**
 * @brief  SVPWM计算函数、根据静止二相坐标系下的电压向量，计算出PWM中心对齐模式下U、V、W三相的接通时间，即脉冲宽度。
 *         该函数需要一个标记PWM周期长度的宏定义 SVPWM_PERIOD ，在本例中PWM频率为15KHz、周期为5600个单位。
 *         注意：仅仅适用于PWM中心对齐模式的应用场景。
 * @param  input 被变换的二相静止电压向量
 * @param  modulation SVPWM调制度，表示了期望输出的大小
 * @param  output 输出的SVPWM三相脉冲宽度（PWM中心对齐模式下）
 * @retval 
 */
void SVPWM(Vector2 *input, float modulation, Vector3 *output){
    
    /* 判断扇区 */
    float alpha = input->x1;
    float beta  = input->x2;
    float beta_div_sqrt3 = beta * SQRT3_3_NUM;  /* 计算 beta/sqrt(3) */
    FOC8BitsNumber sector;

    /* beta > 0 在 1、2、3 扇区 */
    /* beta < 0 在 4、5、6 扇区 */
    /* alpha 与 -beta/sqrt(3) 和 beta/sqrt(3) 的关系可以区分 1 4、2 5、3 6 扇区 */
    if(beta>=0){
        if(alpha>beta_div_sqrt3){
            sector = 1;
        }else{
            if(alpha>-beta_div_sqrt3){
                sector = 2;
            }else{
                sector = 3;
            }
        }
    }else{
        if(alpha>=-beta_div_sqrt3){
            sector = 6;
        }else{
            if(alpha>beta_div_sqrt3){
                sector = 5;
            }else{
                sector = 4;
            }
        }
    }

    /* 计算电压基矢量 */
    /* 计算SVPWM脉冲宽度：先计算零矢量T7，然后依次累加出另外两个基矢量 */
    float U_1, U_2;
    float Tu, Tv, Tw;
    switch (sector) {
        /* 扇区1  变换矩阵为             */
        /*        |  1  -3^0.5/3    |    */
        /*        |  0   3^0.5*2/3  |    */
        case 1:
            U_1 = alpha - beta_div_sqrt3;   /* U 0 0 */
            U_2 = 2.0f * beta_div_sqrt3;    /* U V 0 */
            Tw = (1.0f - modulation * (U_1 + U_2)) * SVPWM_PERIOD * 0.5f;
            Tv = modulation * U_2 * SVPWM_PERIOD + Tw;
            Tu = modulation * U_1 * SVPWM_PERIOD + Tv;
            break;

        /* 扇区2  变换矩阵为             */
        /*        |  1   3^0.5/3    |    */
        /*        | -1   3^0.5/3    |    */
        case 2:
            U_1 = alpha + beta_div_sqrt3;  /* U V 0 */
            U_2 = -alpha + beta_div_sqrt3; /* 0 V 0 */
            Tw = (1.0f - modulation * (U_1 + U_2)) * SVPWM_PERIOD * 0.5f;
            Tu = modulation * U_1 * SVPWM_PERIOD + Tw;
            Tv = modulation * U_2 * SVPWM_PERIOD + Tu;
            break;

        /* 扇区3  变换矩阵为             */
        /*        |  0   3^0.5*2/3  |    */
        /*        | -1  -3^0.5/3    |    */
        case 3:
            U_1 = 2.0f * beta_div_sqrt3;   /* 0 V 0 */
            U_2 = -alpha - beta_div_sqrt3; /* 0 V W */
            Tu = (1.0f - modulation * (U_1 + U_2)) * SVPWM_PERIOD * 0.5f;
            Tw = modulation * U_2 * SVPWM_PERIOD + Tu;
            Tv = modulation * U_1 * SVPWM_PERIOD + Tw;
            break;

        /* 扇区4  变换矩阵为             */
        /*        | -1   3^0.5/3    |    */
        /*        |  0  -3^0.5*2/3  |    */
        case 4:
            U_1 = -alpha + beta_div_sqrt3; /* 0 V W */
            U_2 = -2.0f * beta_div_sqrt3;  /* 0 0 W */
            Tu = (1.0f - modulation * (U_1 + U_2)) * SVPWM_PERIOD * 0.5f;
            Tv = modulation * U_1 * SVPWM_PERIOD + Tu;
            Tw = modulation * U_2 * SVPWM_PERIOD + Tv;
            break;

        /* 扇区5  变换矩阵为             */
        /*        | -1  -3^0.5/3    |    */
        /*        |  1  -3^0.5/3    |    */
        case 5:
            U_1 = -alpha - beta_div_sqrt3; /* 0 0 W */
            U_2 = alpha - beta_div_sqrt3;  /* U 0 W */
            Tv = (1.0f - modulation * (U_1 + U_2)) * SVPWM_PERIOD * 0.5f;
            Tu = modulation * U_2 * SVPWM_PERIOD + Tv;
            Tw = modulation * U_1 * SVPWM_PERIOD + Tu;
            break;
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

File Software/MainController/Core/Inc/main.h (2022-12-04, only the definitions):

#define PWM_PEROID (CKTIM/(2*PWM_FREQ))
#define CKTIM 168000000
#define PWM_FREQ 15000
#define OLED_CS_Pin GPIO_PIN_13
#define OLED_CS_GPIO_Port GPIOC
#define SPI_SDI_Pin GPIO_PIN_6
#define SPI_SDI_GPIO_Port GPIOA
#define SPI_SDO_Pin GPIO_PIN_7
#define SPI_SDO_GPIO_Port GPIOA
#define M1_CS_Pin GPIO_PIN_12
#define M1_CS_GPIO_Port GPIOB
#define M0_EN_Pin GPIO_PIN_10
#define M0_EN_GPIO_Port GPIOC
#define M1_EN_Pin GPIO_PIN_11
#define M1_EN_GPIO_Port GPIOC
#define M0_CS_Pin GPIO_PIN_12
#define M0_CS_GPIO_Port GPIOC
#define FnLED_Pin GPIO_PIN_2
#define FnLED_GPIO_Port GPIOD
#define SPI_SCK_Pin GPIO_PIN_3
#define SPI_SCK_GPIO_Port GPIOB

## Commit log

2021-12-08 增加了硬件部分
    [FOC_Controller.SchDoc, FOC_Controller_BOM.xlsx, FOC_Driver.SchDoc]
2021-12-08 修改了README
2021-12-08 补充了工程文件
    [FOC_Controller_PCB.PrjPcb]
2021-12-12 修改README中的制作进度
2022-01-03 补充了焊接完成图，在README中新增了问题说明
2022-01-03 补充了问题说明
2022-01-03 新建点灯代码工程
2022-01-13 完成屏幕驱动的重构和在README中补充了硬件BUG
2022-01-13 补充控制器尺寸参数
2022-01-13 修改了README的日期和跳转链接
2022-01-13 修改了README跳转连接
2022-02-26 补充DRV8303配置项、增加SPI线设备、增加USB驱动
2022-03-02 完成命令解析模块
2022-03-05 DRV8303的SPI通信握手测试成功
2022-03-31 微调了USB驱动
2022-12-04 增加了部分FOC算法、快速SIN函数；增加了电机0的驱动配置；修复数据上报BUG和一点小问题。
2022-12-04 补充了新增FOC算法的说明

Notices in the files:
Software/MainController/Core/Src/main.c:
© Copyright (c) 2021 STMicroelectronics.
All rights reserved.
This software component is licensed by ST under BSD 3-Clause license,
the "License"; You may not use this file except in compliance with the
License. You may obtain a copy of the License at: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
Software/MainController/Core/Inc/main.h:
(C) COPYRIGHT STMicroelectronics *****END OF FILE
